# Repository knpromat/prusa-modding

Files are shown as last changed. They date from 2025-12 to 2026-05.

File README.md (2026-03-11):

# Wstęp

Po modyfikacjach nasza drukarka 3D korzysta z firmware [klipper](https://www.klipper3d.org/) co zwiększa jej możliwości i prędkość druku.

Szczeguły procesu modyfikacji można znaleźć [tutaj](./doc/prusa-mod-instruction.pdf)

# Intrukcja Obsługi

> [!caution]
> Druk bezpośrednio z karty w drukarce niestety nie jest już możliwy. Należy skorzystać z metody opisanej poniżej!

## Opis ogólny

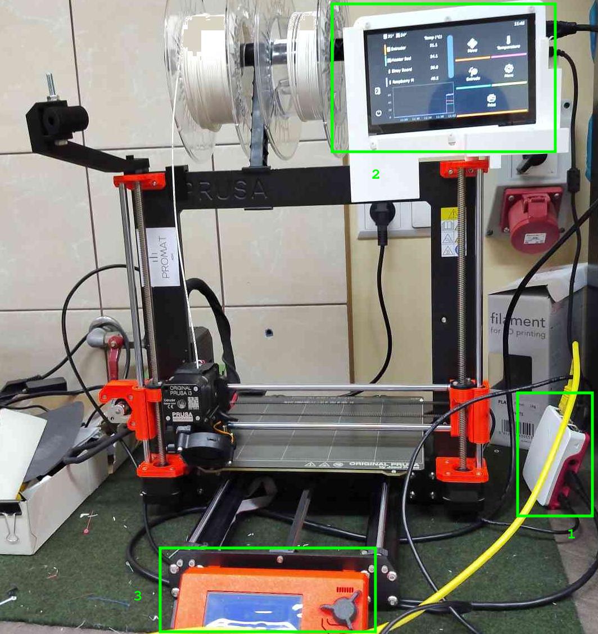
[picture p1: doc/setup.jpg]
Drukarka po modyfikacji


Powyższe zdjęcie przedstawia +/- obecny stan drukarki z oznaczonymi elementami:
1. Raspberry Pi - odpowiada za sterowanie drukarką
2. Ekran dotykowy KlipperScreen - wyświetla GUI (coś na kształt starego ekranu i pokrętła). Można z niego odpalać wydruki, ładować/wyładowywać filament e.t.c.
3. Stare kontrolki drukarki - nadal da się ich do czegoś używać ale np. nie da się już puszczać wydruków itd.

## Metody uploadowania gcode

### Metoda 1 - przez WebGUI (MainSail)
Ta metoda wymaga połączenia się z Raspberry przez sieć. Można to zrobić na dwa sposoby
1. Przez hotspot (prusa-promat)*
2. Po kablu ethernet (trzeba u siebie odpalić serwer DHCP)

Następnie:
- Wchodzimy na stronę http://promatprusa.local (ewentualnie po IP)
- Wpisujemy login+hasło do NGNIX
- Dostajemy dashboard mainsaila:

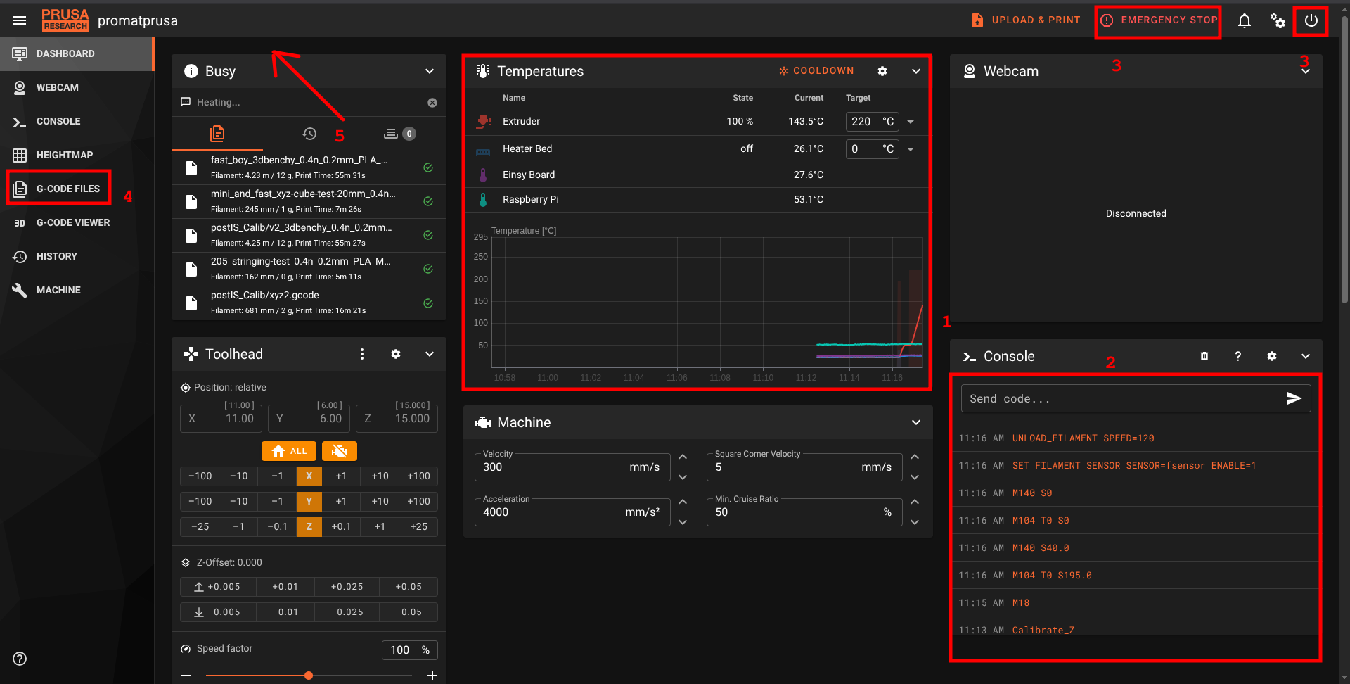
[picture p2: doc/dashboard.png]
Mainsail dashboard


1. Wykres temperatury
2. Konsola (można wysyłać GCode bezpośrednio do drukarki)
3. Emergency Stop (gdyby coś się działo złego) - natychmiast zatrzymuje drukarke (tak jakby wcisnąć ten guzik pod pokrętłem)
4. Tutaj można restartować różne komponenty systemu (sam klipper, całe raspberry, moonraker e.t.c.)
5. Tutaj można wrzucać pliki z GCode

- przechodzimy do zakładku `5`

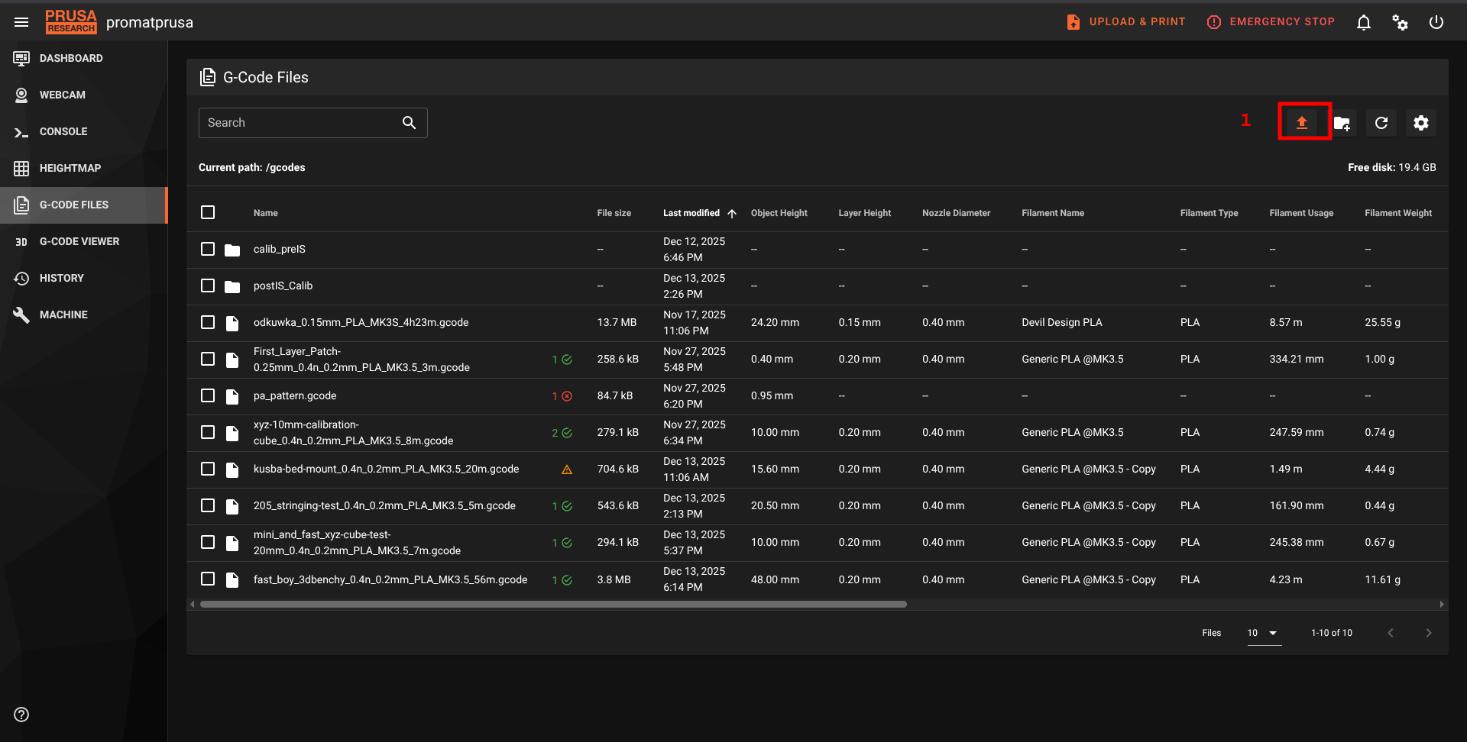
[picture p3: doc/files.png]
File manager


Przy pomocy `1` możemy wrzucić pliki GCode.

### Metoda 2 - przez port USB na malince
1. Należy wpiąć pendrive lub czytnik kart SD do malinki
2. Pliki w ten sposób pokażą się w folderze `external_storage`

> [!important]
> Pliki przesłane w ten sposób **NIE** zostaną przesłane i nie należy wyciągać pendrive aż do momentu zakończenia druku.

## Obsługiwane slicer'y

> [!note]
> obecnie development prowadzimy na Orca Slicer. Config do Prusa Slicer nie był ostatnio aktualizowany i wymaga sprawdzania.

<details><summary>Orca Slicer</summary>

### Instalacja i wstępna konfiguracja Orca SLicer

1. Pobierz Orca Slicer: https://orca-slicer.com/
2. Uruchom program
3. Pobierz [plik konfiguracyjny](./end-user-config/orca_slicer/PROMAT - Prusa MK3S+ Klipper.orca_printer)
4. zaimportuj konfiguracje do Orca SLicer (File -> Import -> Import Configs)

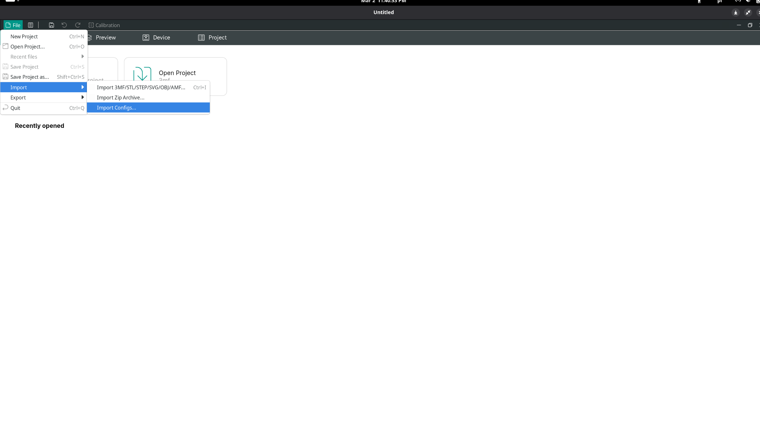
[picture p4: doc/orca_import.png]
import config


</details>

<!--
<details><summary>Prusa Slicer</summary>

### Aktualizacja profilu w prusa-slicer

> [!warning]
> sprawdzić temperatury!

Ponieważ używamy klippera, musimy zaktualizować profil drukarki w prusa-slicerze. Najnowszy profil znajduje się [tutaj](./end-user-config/prusa_mk3s+_klipper.ini).

![How to update the profile](./doc/profile-update.png)

</details>
-->

## Uruchamianie wydruków

> [!important]
> Upewnij się, że masz aktualny profil slicera! [Najnowsza wersja znajduje się tutaj](./end-user-config/prusa_mk3s+_klipper.ini)

### Metoda 1 - z WebGUI

- Wybieramy plik w eksploratorze plików i wciskamy `Print`

### Metoda 2 - z ekranu dotykowego KlipperScreen

Na ekranie wybieramy Print -> <nazwa pliku> -> Print

# TODO

- [ ] podpiąć rpi do sieci
- [ ] dodać możliwość uploadów gcode bezpośrednio ze slicera
- [ ] dać issue do https://github.com/xbst/KUSBA/blob/main/Docs/v2-Firmware.md o koniecznośći zmiany docelowego mikrokontrolera w nowym klipperze

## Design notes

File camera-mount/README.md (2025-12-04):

# Uchwyt do kamerki
Płytka jest przykręcana zamiast tylnego panelu obudowy.
Ramie jest przykręcane do górnej części ramy prusy
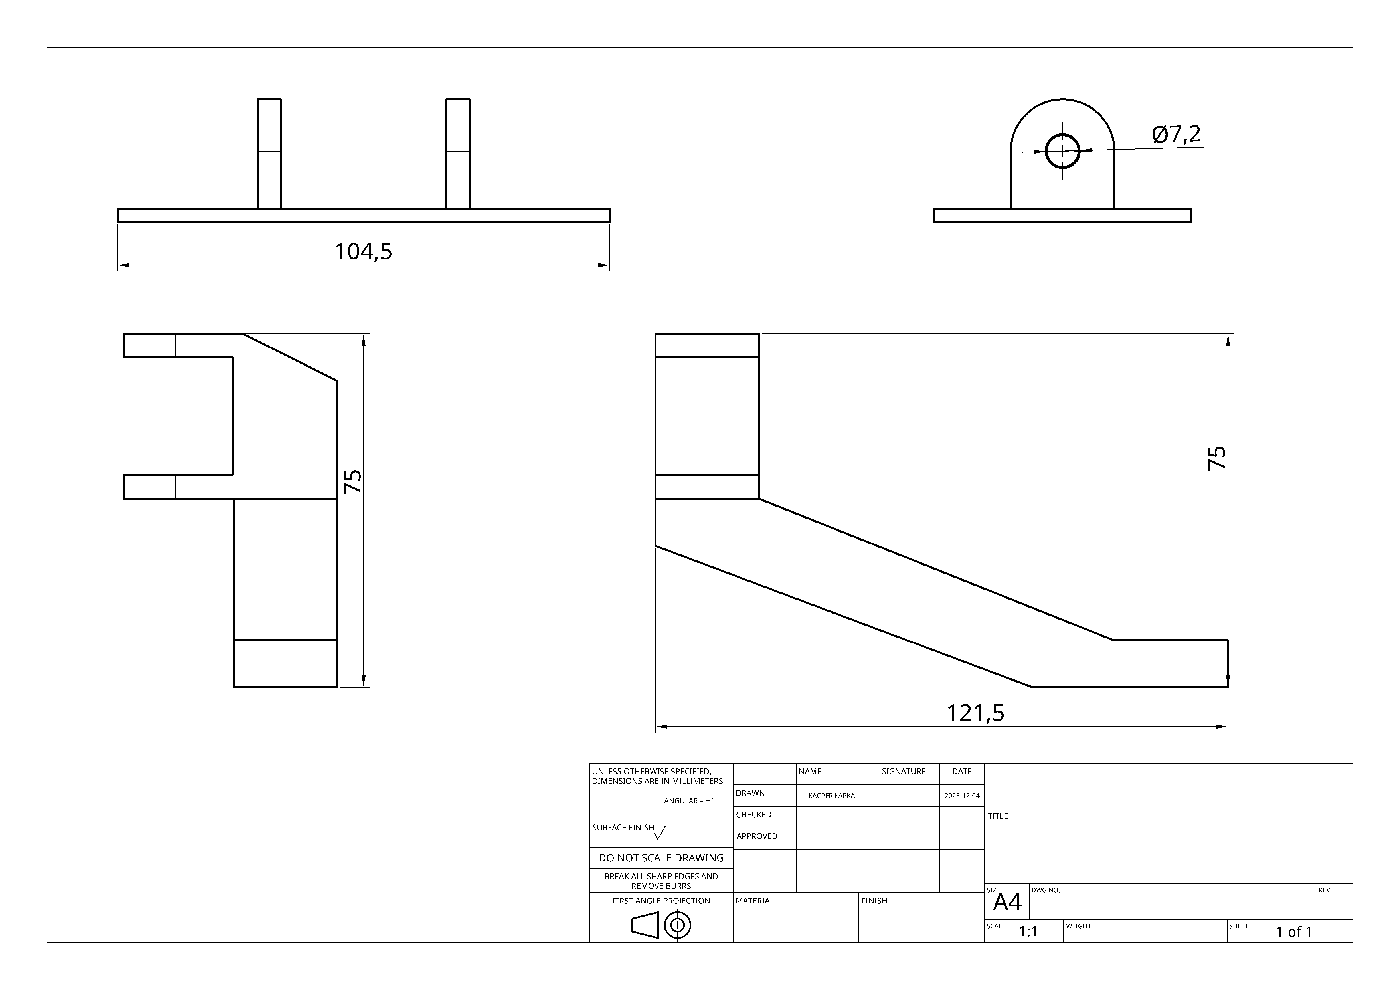
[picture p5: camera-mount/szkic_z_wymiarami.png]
szkic


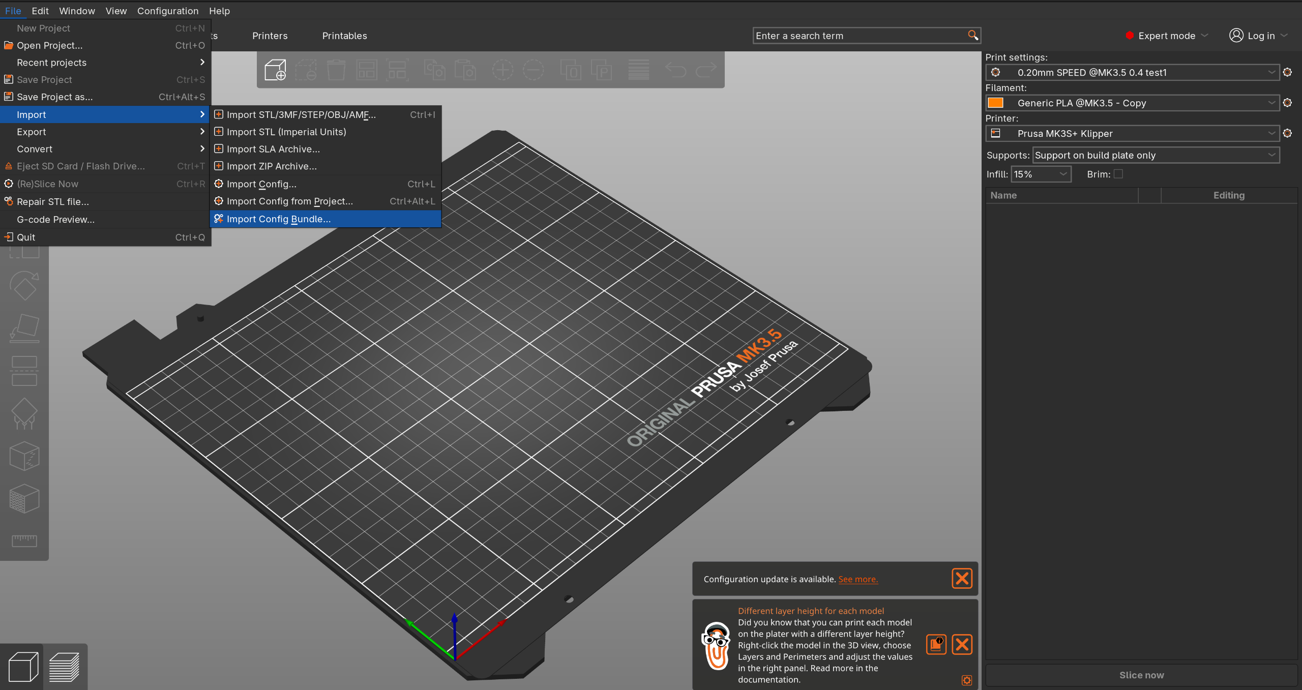
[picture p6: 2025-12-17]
doc/profile-update.png

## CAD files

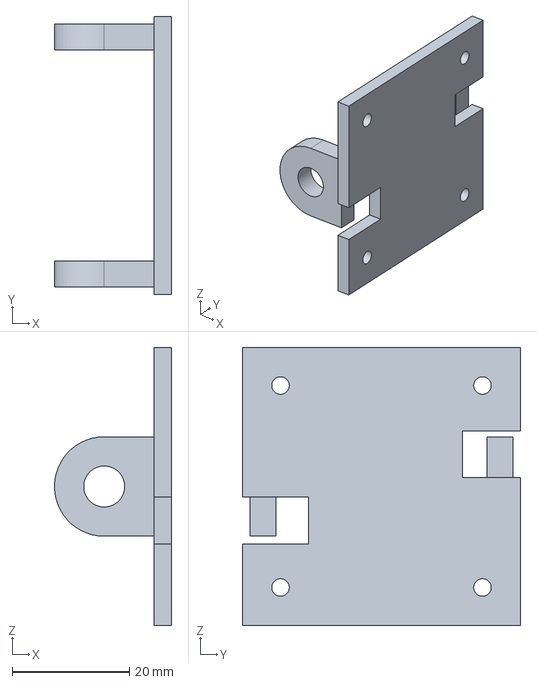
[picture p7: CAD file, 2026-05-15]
camera-mount/iduino_cam_adapter.FCStd
20.0 x 47.5 x 47.5 mm

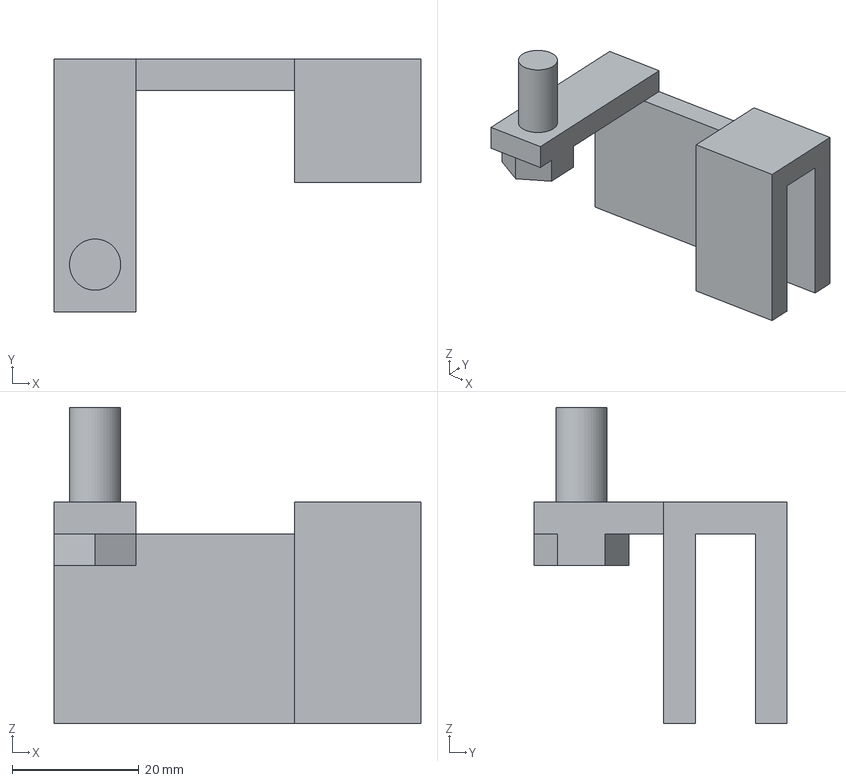
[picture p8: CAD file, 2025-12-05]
camera-mount/prusa_uchwyt.step
58.0 x 40.0 x 50.0 mm

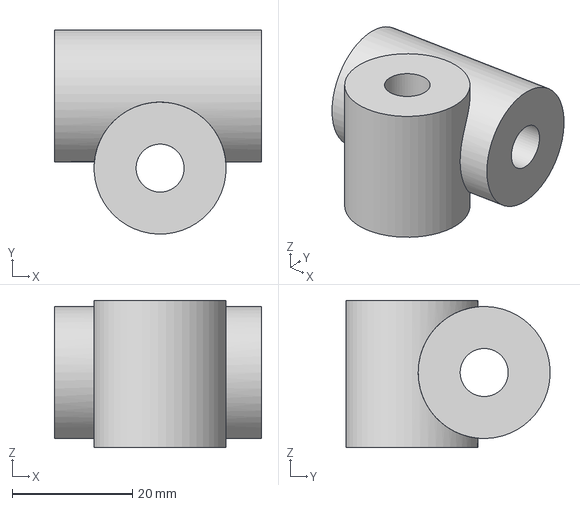
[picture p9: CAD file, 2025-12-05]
camera-mount/lacznik.step
34.5 x 34.0 x 24.5 mm

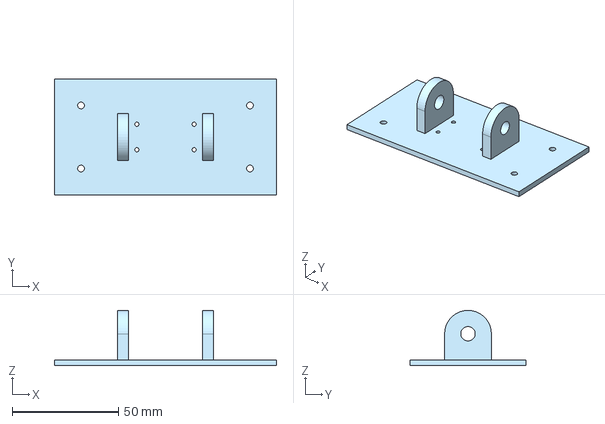
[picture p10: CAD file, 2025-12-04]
camera-mount/obudowa_do_kamerki.step
104.5 x 54.5 x 26.0 mm

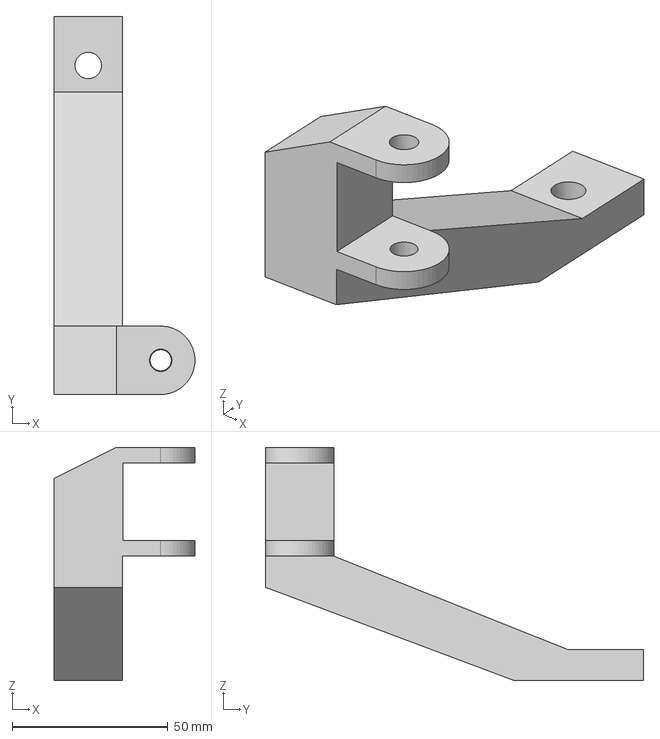
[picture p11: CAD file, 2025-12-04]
camera-mount/ramie_do_kamerki.step
45.3 x 121.5 x 75.0 mm

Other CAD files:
camera-mount/prusa_uchwyt.FCStd

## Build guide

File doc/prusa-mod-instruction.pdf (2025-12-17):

## Upgrade Prusy

- Model: Prusa i3 MK3S+
- Tutorial: https://github.com/charminULTRA/Klipper-Input-Shaping-MK3S-Upgrade

## Jaki cel chcemy osiągnąć

Chcemy zrobić upgrade naszej drukarki aby działała na firmware klipper.

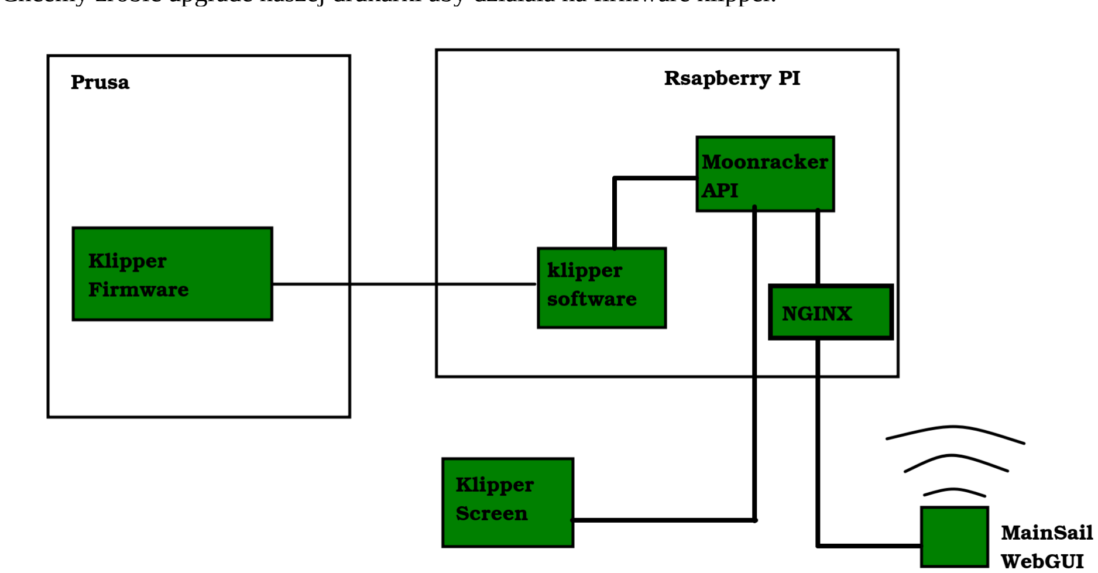
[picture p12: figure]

## Zalety

- Bezpośrednia możliwość kontroli zdalnej przez Raspberry Pi (dalej rpi) przez:
- lokalnie hostowaną sieć WiFi
- sieć wydziałową (albo z zewnątrz przez AGHowy VPN)
- ekran KlipperScreen
- Możliwość wykorzystania technologii Input Shaping – szybszy druk
- Integracja kamery

## Wady

- Konieczność pracy przy samej drukarce około 5-20 godzin. W trakcie prac nie będzie można nic drukować (dopuki flash+kalibracja nie zakończą się powodzeniem).
- (docelowo możńa wyeliminować) utrata możliwości kontroli drukarki przez wbudowany ekran/pokrętło (musimy zflashować klippera; wtedy możliwość kontroli tylko przez rpi)

## Koszty

Opis | URL | Cena [PLN]
Akcelerometr - wykorzystywany tylko w czasie kalibracji Input Shaping, będzie można wykorzystać w przyszłości do innych drukarek | https://pl.aliexpress.com/item/1005007664753714.html (https://pl.aliexpress.com/item/1005007664753714.html) | 52.79
Ekran zewnętrzny do instalacji KlipperScreen | https://pl.aliexpress.com/item/32917024241.html (https://pl.aliexpress.com/item/32917024241.html) | ~60

## Plan Działania

1. Instalacja mainsailOS na Raspberry https://docs-os.mainsail.xyz/
2. skonfigurowanie kamery https://docs.mainsail.xyz/overview/settings/webcams
3. skonfigurowanie accesspointa na RPI
4. ustawienie credentiali na NGINX
5. zdesignowanie i wydruk uchwytu na kamerę
6. Zmodyfikacja presetu w prusa slicerze (potem wrzucimy gdzieś te configi żeby każdy z koła miał do nich dostęp). W tym celu kopiujemy preset dla MK3.5 następnie modyfikujemy sutawienia (opisane na githubie) [daję to przed flashowaniem bo teoretycznie nie trzeba mieć do tego klippera na drukarce]
7. wydruk uchwytu do mocowania akcelerometru i ogarnięcie montażu https://www.printables.com/model/495459-kusba-accelerometer-universal-mount
8. flashowanie klippera jako firmware
1. Odczyt Z-Offsetu z ustawień
2. pełny odczyt obecnego EPROMu https://help.prusa3d.com/article/prusa-firmware-specific-g-codecommands_112173 (https://help.prusa3d.com/article/prusa-firmware-specific-g-code-commands_112173)
3. dodatkowy odczyt kalibracji (M503)
4. flashowanie (jak w instrukcji). W razie potrzeby można przywrócić stock wraz z ustawieniami.
9. Weryfikacja (BEZ ENDSTEPs) https://www.klipper3d.org/Config_checks.html
10. Kalibracja https://ellis3dp.com/Print-Tuning-Guide/articles/index_tuning.html (na pewno trzeba zrobić extruder calibration i pressure advancement, ale inne też się przyda)
11. akrywacja input shaping
1. wydruk https://www.printables.com/model/724132-kusba-adxl345-print-on-bed-mount
2. aktualizacja firmware w akcelerometrze: https://github.com/xbst/KUSBA/blob/main/Docs/v2-Firmware.md (https://github.com/xbst/KUSBA/blob/main/Docs/v2-Firmware.md)
3. dokonanie kalibracji (jak w instrukcji)
12. ponowna kalibracja (jak wyżej) – głównie chodzi o PA
13. dogadanie się z wydziałowym informatykiem aby wystawić RPI w sieci wydziałowej
14. ewentualny montaż dodatkowego ekranu dotykowego do kontroli klippera.

Na czerwono zaznaczony tekst to kroki procedury w których drukarka jest w pełni niezdolna do jakichkolwiek wydruków. Na fioletowo zaznaczyłem kroki w których drukować się da ale jakość będzie słaba.

## Linki

- https://www.klipper3d.org/
- https://docs.mainsail.xyz/ bundle OS+WebGUI
- https://klipperscreen.readthedocs.io/en/latest/
- https://marlinfw.org/docs/gcode/G005.html
- https://help.prusa3d.com/article/prusa-firmware-specific-g-code-commands_112173 Odczyt EPROM

- https://help.prusa3d.com/downloads stock firmware

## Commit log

2025-12-04 Added .step and drawing for cam holder
    [obudowa_do_kamerki.step, ramie_do_kamerki.step]
2025-12-05 Add arm and case connector
    [lacznik.step]
2025-12-05 camera mount: add printer mount for the holder
    [prusa_uchwyt.FCStd, prusa_uchwyt.step]
2025-12-17 readme: add intro, TODO and begin tutorial assembly
2025-12-19 Remove custom marlin G-code
2026-01-16 Update README.md
    - Indicate that printing through usb is now possible
2026-01-22 Update slicer config - disable emitting temperature commands, because klipper macro do that and it is faster without it
2026-03-11 orca slicer: merge My Supports preset intoi main 0.2 preset
    my supports are better because they are not soldered to the object
2026-04-29 orca_slicer: add Brrrr profile
    - added as separate printer because hardware limits had to be changed
2026-05-15 feat(camera mount): add adapter for our new camera
    After the old camera has died and we bought the new one
    (iduino somethingsomething) I've tesigned this part to make use of our
    old mount just changing the camera mounting part itself
    [iduino_cam_adapter.FCStd]
